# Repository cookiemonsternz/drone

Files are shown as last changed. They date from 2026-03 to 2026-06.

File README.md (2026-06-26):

# F<sub>~ish</sub>PV

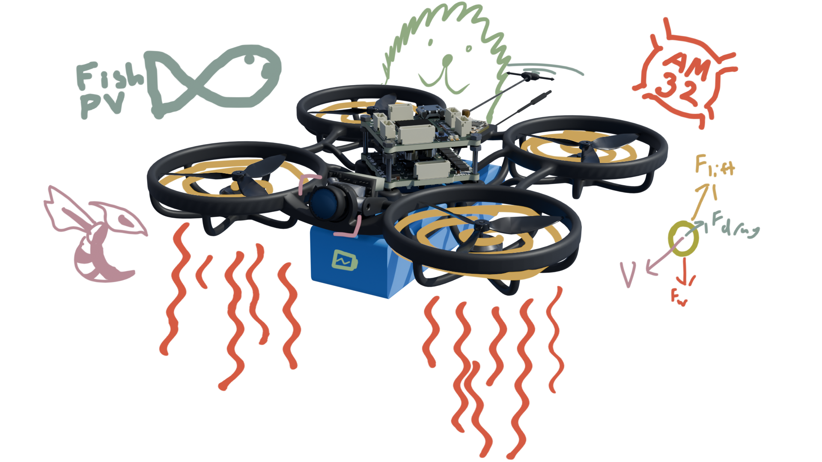
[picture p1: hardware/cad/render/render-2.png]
Render

_Tinywhoop drone with custom ESC, FC, and frame._

## What?

F<sub>\~ish</sub>PV is a open source, custom stack, 75mm tinywhoop drone design.
It utilises AM32 for the ESC firmware and Betaflight for the flight controller. 

Custom components include a from-scratch frame, designed for 3d printing (in HP-12-CF filament), a fully custom 15A ESC, and a custom FC. 

**The ESC:**
- 15A Continuous
- 20A Peak for 5s (unverified :O)
- 2S Battery (only)
- AM32 Firmware
- DSHOT Communication + Voltage telemetry
- Current Sense
  
**The FC:**
- STM32F405
- OSD: MAX7456
- IMU: ICM-42688-P
- 128Mbit blackbox
- USB DFU
- 2S Battery (only)
- BEC: 5V/0.5A Max
- Mounting: 25.5x25.5
- Dimensions: 28.3x28.3x10
- UART: 1, 4, 5
- Buzzer!

## Why?

To be honest a lot of this project was just for my own learning, but I also wanted to make a drone that could be generally cheaper than buying prebuilt components. I've somewhat achieved this, with a net cost of ~$300 USD, but obviously this cost is higher due to lack of bulk pricing. Unfortunately, some parts I wanted to design from scratch proved to be infeasible within the scope of this project (namely vtx and vrx) so that has driven the total cost up slightly.

Aside from that, drones are cool, and tinywhoops especially so. The main benefit in my opinion is the crashability. The size makes it much more feasible to use alternative manufacturing options. As I mentioned earlier, I designed this with HP-12-CF filament in mind, but HP-12 MJF Nylon is also a very feasible option that could potentially be quite durable (I have simulated both, but it is worth noting that the CF simulations will not be entirely accurate due to the weakness along layer lines not being modelled).

## How to use?

The drone assembly should be reasonably straightforward, I have provided a wonderful exploded diagram that should help significantly:

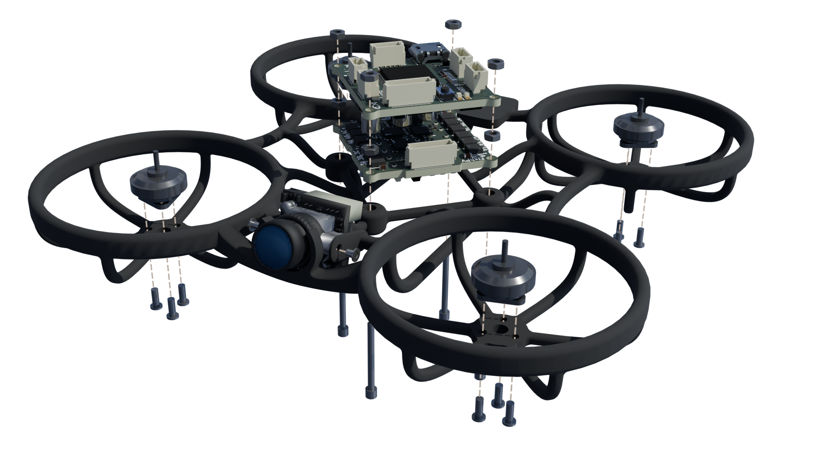
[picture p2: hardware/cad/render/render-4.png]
Exploded Diagram

Feel free to assemble it how you see fit, I'll likely change some things in the future but I'd like to try this configuration for now.

For wiring, theres this handy diagram. A lot of it just uses jst-sh connectors (as conformant to the [Betaflight Connector Standard](https://betaflight.com/docs/development/manufacturer/connector-standard)).

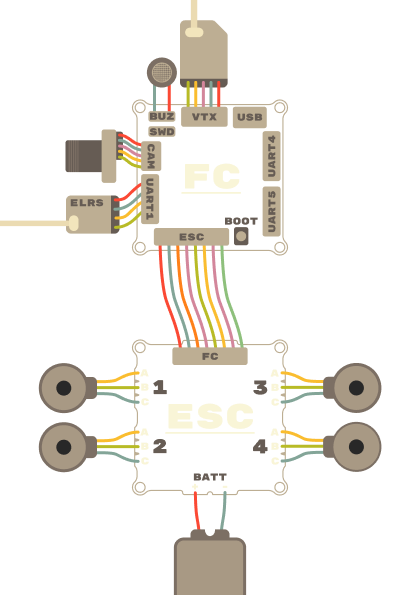
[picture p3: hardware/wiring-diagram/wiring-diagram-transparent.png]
Wiring Diagram


The ELRS receiver and vtx module can be attached however you see fit. I have included a mounting plate, and myself intend to use hot glue but velcro, etc. are also options.

Aside from the physical assembly, the FC and ESC must be flashed as outlined below or in the respective folders in **firmware/**. As I didn't want to do a bunch of pull requests for a likely one off design, I have provided compiled versions of the firmware. If you want to compile yourself, check out my forks of [Betaflight](https://github.com/cookiemonsternz/betaflight) and [AM32](https://github.com/cookiemonsternz/AM32). AM32 was built using github actions, and Betaflight was built locally using WSL as outlined in [the documentation](https://betaflight.com/docs/development#development).

### ESC Firmware

The esc runs on AM32, an open source ESC firmware which manages motor control, communication via dshot, and telemetry.

#### Bootloader

First of all, we need to install the bootloader onto each of the chips. For each chip, connect via the exposed swd/io interface, as outlined in the following table, and flash the bootloader hex file from **firmware/esc/bootloader/**

| MCU | SWDIO | SWDCLK |
|-----|---|---|
| 1 | TP1 | TP2 |
| 2 | TP3 | TP4 |
| 3 | TP6 | TP5 |
| 4 | TP8 | TP7 |

#### Firmware

Next connect the flight controller (which should be flashed before this step),
visit [am32 configurator](https://am32.ca/) and upload the firmware from **firmware/esc/**

---

### FC Firmware

Installation follows the same procedure as pretty much any flight controller.
Visit [Betaflight Configurator](https://app.betaflight.com/) and select firmware flasher. 

At the bottom of the screen, press load local:
Configurator
Upload the hex file and then hit flash!

That's it, should be all configured (maybe) but I'd reccomend going through and doing the regular adjustments and calibration.

## Renders

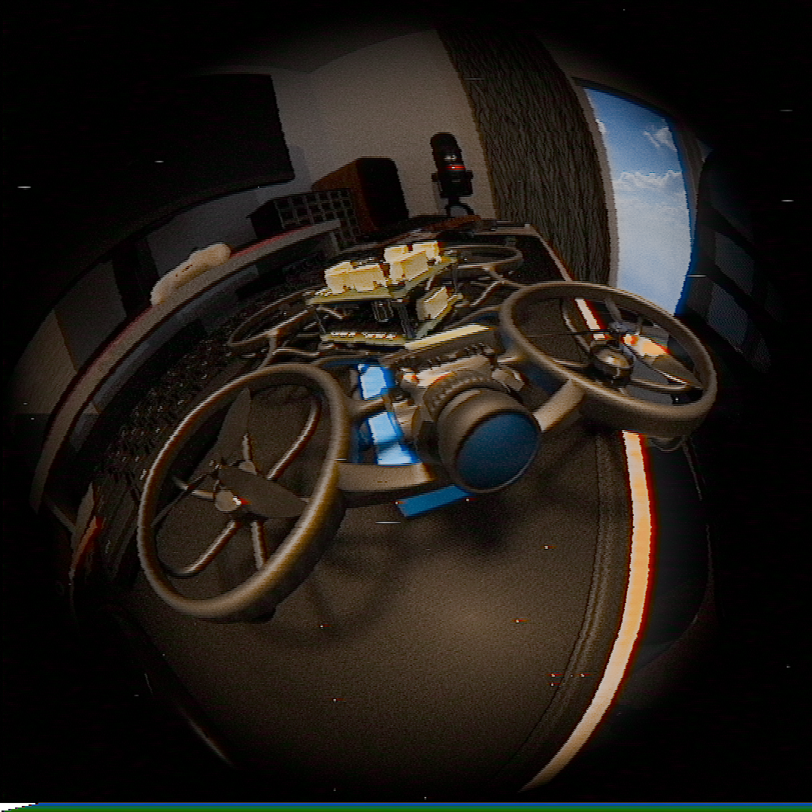
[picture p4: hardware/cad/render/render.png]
Render 1

Render 2
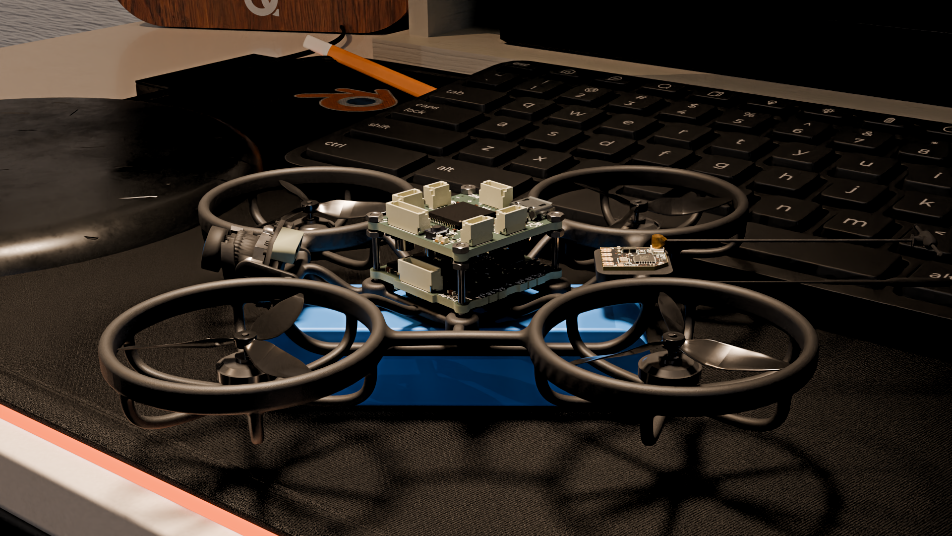
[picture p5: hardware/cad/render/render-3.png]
Render 3


## Zine Page

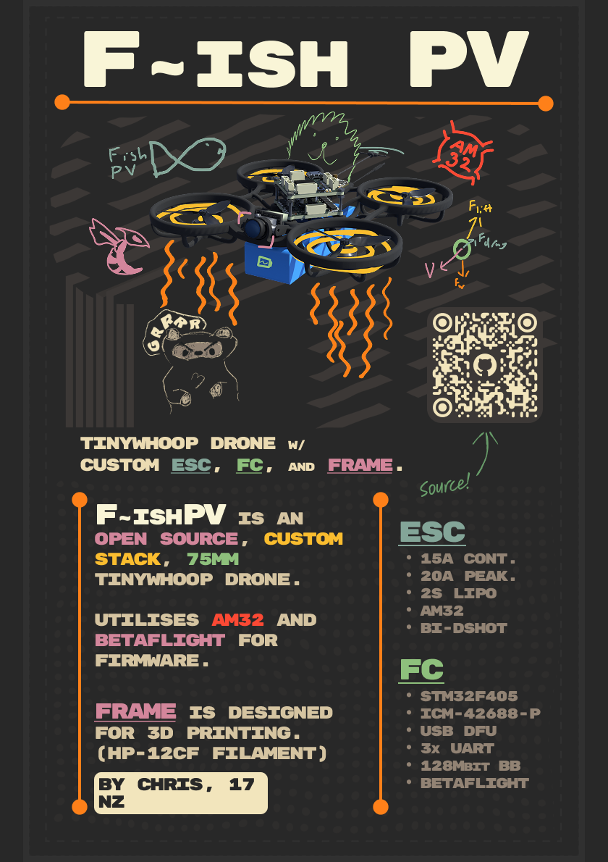
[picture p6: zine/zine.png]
Zine Page


## Simulations

I ran a handful of simulations in FreeCAD, and these are just a small sample of the results I got. 

First up, a collision where the battery is impacted. Think the drone just dropping onto the ground. This is for a collision at approximately 50km/h assuming a collision time of 25ms and a net mass of around 250g (so probably a bit extreme), to be specific, I modelled a force of 150N.
Battery collision
As you can see, there is even deflection across all four mounting posts for the FC/ESC stack, which will result in minimal tensile strain on the PCBs (which is the typical cause of damage).

Another type of collision I modelled is just a collision directly to the prop guards. Again, a 150N force which would be ~50km/h as mentioned above.
Prop guard collision
There is a lot of displacement on the prop guard but it is effectively dissipated and won't have much impact on the electronics, which is the main thing to be worried about. 
For this specific impact, I would be reasonably worried about damage to the frame, but for most crashes (which are probably not at 50km/h) it should be perfectly fine.

Many more simulations at different loads and also modelling the HP-12 MJF material can be found [here](https://github.com/cookiemonsternz/drone/blob/main/journals/journal-14-05-2026.md).

## BOM

| Desc | Value | Package | Link | Num | Needed | MOQ | MOQ Price | Net Price | Running Total |
|---|---|---|---|-----|---|-----|---|---|---|
| **Capacitors** | | | | | | | | | |
| 10nF Ceramic Cap, 0402 | 10nF | 0402 | https://www.lcsc.com/product-detail/C15195.html | 1 | 1 | 100 | $0.16 | $0.16 | $0.16 |
| 22nF Ceramic Cap, 0402 | 22nF | 0402 | https://www.lcsc.com/product-detail/C1532.html | 2 | 2 | 100 | $0.21 | $0.21 | $0.37 |
| 100nF Ceramic Cap, 0402 | 100nF | 0402 | https://www.lcsc.com/product-detail/C1525.html | 44  | 44 | 100 | $0.15 | $0.15 | $0.52 |
| 1uF Ceramic Cap, 0402 | 1uF | 0402 | https://www.lcsc.com/product-detail/C52923.html | 4 | 4 | 100 | $0.4 | $0.40 | $0.92 |
| 2.2uF Ceramic Cap, 0402 | 2.2uF | 0402 | https://www.lcsc.com/product-detail/C12530.html | 3 | 3 | 100 | $0.32 | $0.32 | $1.24 |
| 4.7uF Capacitors, 0603 | 4.7uF | 0603 | https://www.lcsc.com/product-detail/C19666.html | 4 | 4 | 10  | $0.11 | $0.11 | $1.35 |
| 22uF Capacitors, 0603 | 22uF | 0603 | https://www.lcsc.com/product-detail/C86295.html | 4 | 4 | 10  | $0.16 | $0.16 | $1.51 |
| 22uF Capacitors, 0805 | 22uF | 0805 | https://www.lcsc.com/product-detail/C29277.html | 2 | 2 | 10  | $0.21 | $0.21 | $1.72 |
| 22uF Electrolytic Cap, SMD | 22uF | SMD,D4xL5.4mm  | https://www.lcsc.com/product-detail/C335975.html | 2 | 2 | 20  | $0.48 | $0.48 | $2.20 |
| 47uF Electrolytic Cap, SMD | 47uF | SMD,D4xL5.4mm  | https://www.lcsc.com/product-detail/C87853.html | 2 | 2 | 20  | $0.53 | $0.53 | $2.73 |
| **Resistors** | | | | | | | | | |
| 22R Resistors, 0402 | 22r | 0402 | https://www.lcsc.com/product-detail/C2906914.html | 26  | 26 | 100 | $0.07 | $0.07 | $2.80 |
| 75R Resistor, 0402 | 75? | 0402 | https://www.lcsc.com/product-detail/C25133.html | 4 | 4 | 100 | $0.09 | $0.09 | $2.89 |
| 1k Resistor, 0402 | 1k? | 0402 | https://www.lcsc.com/product-detail/C11702.html | 17  | 17 | 100 | $0.11 | $0.11 | $3.00 |
| 2.2k Resistor, 0402 | 2.2k? | 0402 | https://www.lcsc.com/product-detail/C25879.html | 3 | 3 | 100 | $0.10 | $0.10 | $3.10 |
| 10k Resistor, 0402 | 10k? | 0402 | https://www.lcsc.com/product-detail/C25744.html | 6 | 6 | 100 | $0.13 | $0.13 | $3.23 |
| 100k Resistor, 0402 | 100k? | 0402 | https://www.lcsc.com/product-detail/C25741.html | 4 | 4 | 100 | $0.09 | $0.09 | $3.32 |
| 10k Resistor Arrays, 0603x4 | 10k | 0603x4 | https://www.lcsc.com/product-detail/C110924.html | 6 | 6 | 50  | $0.55 | $0.55 | $3.87 |
| 124k Voltage Div Resistor, 0603 | 124k | 0603 | https://www.lcsc.com/product-detail/C2933136.html | 1 | 1 | 100 | $0.11 | $0.11 | $3.98 |
| 0.5m Shunt Resistor, 1216 | 0.5mr | 1216 | https://www.lcsc.com/product-detail/C2688874.html | 1 | 1 | 1 | $1.01 | $1.01 | $4.99 |
| **Diodes** | | | | | | | | | |
| Red LED | | 0603 | https://www.lcsc.com/product-detail/C51933292.html | 1 | 1 | 50  | $0.13 | $0.13 | $5.12 |
| Blue LED | | 0603 | https://www.lcsc.com/product-detail/C2288.html | 1 | 1 | 50  | $0.51 | $0.51 | $5.63 |
| Green LED | | 0603 | https://www.lcsc.com/product-detail/C22371297.html | 1 | 1 | 50  | $0.71 | $0.71 | $6.34 |
| Schottky Diode | | SOD-323 | https://www.lcsc.com/product-detail/C191023.html | 2 | 2 | 50  | $0.54 | $0.54 | $6.88 |
| **Connectors** | | | | | | | | | |
| Camera Conn | 3P SH | SMD,P=1mm | https://www.lcsc.com/product-detail/C7430452.html | 1 | 1 | 5 | $0.34 | $0.34 | $7.22 |
| UART Conns | 4P SH | SMD,P=1mm | https://www.lcsc.com/product-detail/C7433440.html | 3 | 3 | 10  | $0.35 | $0.35 | $7.57 |
| VTX Conn | 5P SH | SMD,P=1mm | https://www.lcsc.com/product-detail/C2845373.html | 1 | 1 | 5 | $0.58 | $0.58 | $8.15 |
| ESC Conns | 8P SH | SMD,P=1mm | https://www.lcsc.com/product-detail/C2764202.html | 2 | 2 | 5 | $0.61 | $0.61 | $8.76 |
| USB Micro B Conn | | SMD | https://www.lcsc.com/product-detail/C404969.html | 1 | 1 | 10  | $0.41 | $0.41 | $9.17 |
| **FC** | | | | | | | | | |
| STM32F405 (U1) | | LQFP-64(10x10) | https://www.lcsc.com/product-detail/C15742.html | 1 | 1 | 1 | $3.93 | $3.93 | $13.10 |
| ICM-42668-P : IMU (U2) | | LGA-14(2.5x3)  | https://www.lcsc.com/product-detail/C1850418.html | 1 | 1 | 1 | $12.88 | $12.88 | $25.98 |
| MAX-7456eui+ (U3) | Source: Aliexpress | | https://www.aliexpress.com/item/33005990891.html | 1 | 1 | 1 | $4.28 | $4.28 | $30.26 |
| BL8072CLTR-3.3 (3.3V LDO) (U6) | 3.3V | SOT-223-3 | https://www.lcsc.com/product-detail/C843780.html | 1 | 1 | 5 | $0.99 | $0.99 | $31.25 |
| SGM2212-3.3XKC3G/TR (IMU LDO) (U7) | 3.3V | SOT-223-3 | https://www.lcsc.com/product-detail/C3294699.html | 1 | 1 | 1 | $0.61 | $0.61 | $31.86 |
| W25Q128JVSIQ TR (Flash) (U8) | | SOIC-8-208mil  | https://www.lcsc.com/product-detail/C97521.html | 1 | 1 | 1 | $2.32 | $2.32 | $34.18 |
| TPS62173DSG (5V BEC) (U4, U5) | 5V | WSON-8-EP(2x2) | https://www.lcsc.com/product-detail/C181384.html | 2 | 2 | 1 | $0.93 | $1.86 | $36.04 |
| BMP280 Baro (U10) | | LGA-8(2x2.5) | https://www.lcsc.com/product-detail/C83291.html | 1 | 1 | 1 | $6.90 | $6.90 | $42.94 |
| 27MHz Crystal (Y1) | 27MHz | SMD3225-4P | https://www.lcsc.com/product-detail/C9008.html | 1 | 1 | 10  | $0.77 | $0.77 | $43.71 |
| 8MHz Crystal w/ Caps (Y2) | 8MHz | SMD3213-3P | https://www.lcsc.com/product-detail/C907975.html | 1 | 1 | 5 | $1.05 | $1.05 | $44.76 |
| BEC Inductors (L1, L2) | 2.2uH | 0806 | https://www.lcsc.com/product-detail/C695610.html | 1 | 1 | 5 | $0.82 | $0.82 | $45.58 |
| BOOT Button (SW2) | | SMD,4x3mm | https://www.lcsc.com/product-detail/C720477.html | 1 | 1 | 10  | $0.54 | $0.54 | $46.12 |
| Reverse Pol. Mosfet (Q1) | | SOT-23 | https://www.lcsc.com/product-detail/C15127.html | 1 | 1 | 10  | $0.59 | $0.59 | $46.71 |
| **ESC** | | | | | | | | | |
| 470nH Inductor, 0603 | 470nH | 0603 | https://www.lcsc.com/product-detail/C113132.html | 1 | 1 | 10  | $0.47 | $0.47 | $47.18 |
| Mosfets (SP40N03GNJ) | | PDFN-8L(3x3) | https://www.lcsc.com/product-detail/C22466709.html | 24  | 24 | 5 | $1.05 | $5.25 | $52.43 |
| ESC MCUs (AT32F421G8U7) | | QFN-28-EP(4x4) | https://www.lcsc.com/product-detail/C2765098.html | 4 | 4 | 1 | $0.85 | $3.40 | $55.83 |
| ESC Mosfet Gate Drivers (NSG2065Q) | | QFN-24-EP(4x4) | https://www.lcsc.com/product-detail/C41414478.html | 4 | 4 | 1 | $0.48 | $1.92 | $57.75 |
| Current Sense Amplifier (INA180B2) | | SOT-23-5 | https://www.lcsc.com/product-detail/C2057844.html | 1 | 1 | 1 | $0.26 | $0.26 | $58.01 |
| 8V Regulator (LMR51420YDDCR) | | SOT-23-6 | https://www.lcsc.com/product-detail/C5383002.html | 1 | 1 | 1 | $0.83 | $0.83 | $58.84 |
| 3.3V Regulator (TLV76733DRVR) | | WSON-6(2x2) | https://www.lcsc.com/product-detail/C2848334.html | 1 | 1 | 5 | $1.01 | $1.01 | $59.85 |
| **BOARDS** | | | | | | | | | $59.85 |
| ESC Board + Stencil (JLCPCB) | | | | | | | | $5.29 | $65.14 |
| FC Board + Stencil (JLCPCB) | | | | | | | | $5.21 | $70.35 |
| Frame (JLC3DP, HP-12-CF) | | | | | | | | $5.56 | $75.91 |
| **MODULES** | | | | | | | | | $75.91 |
| ELRS Receiver (RP1 Nano Clone) | | | https://www.aliexpress.com/item/1005005236594556.html | 1 | 1 | 1 | $12.62 | $12.62 | $88.53 |
| CaddX Ant Camera | | | https://www.aliexpress.com/item/1005008798090166.html | 1 | 0 | 1 | $12.99 | $0.00 | $88.53 |
| PandaRC Nano25 VTX | | | https://www.aliexpress.com/item/1005011701933149.html | 1 | 0 | 1 | $18.94 | $0.00 | $88.53 |
| Happymodel RS1102 13500KV Motors | | | https://kiwiquads.co.nz/product/happymodel-rs1102-kv13500-brushless-motor-for-m8-freestyle/ | 4 | 4 | 4 | $11.11 | $44.44 | $132.97 |
| 40mm 1.5mm Shaft Triblade Props | | | https://www.aliexpress.com/item/1005010520091463.html | 4 | 4 | 16  | $6.37 | $6.37 | $139.34 |
| 2s 680mah lipo | | | https://kiwiquads.co.nz/product/betafpv-lava-series-ii-2s-680mah-95c/ | 1 | 1 | 1 | $14.62 | $14.62 | $153.96 |
| Radiomaster T8L | | | https://radiomasterrc.com/products/t8l-radio-controller?variant=47089026465984 | 1 | 1 | 1 | $34.99 | $34.99 | $188.95 |
| TS832 Receiver | | | https://www.aliexpress.com/item/1005012037139433.html | 1 | 0 | 1 | $43.86 | $0.00 | $188.95 |

| Totals (EXCL. VIDEO SYSTEM) | | |
|---|---|---|
| Vendor | Net | W/ Shipping |
| JLCPCB / 3DP | $16.06  | $41.99 |
| LCSC | $55.16  | $55.55 |
| Aliexpress | $23.27  | $22.95 |
| Kiwiquads | $59.05  | $61.96 |
| Radiomaster | $34.99  | $44.99 |
| JLCPCB | $10.50  | $32.06 |
| --- | $199.03 | $259.50 |

## Cad Links

All of the CAD source files can be found on [Onshape](https://cad.onshape.com/documents/5b69b7ad5dc2bcb1a562cae6/w/28cfd389aaff8b3000581458/e/21531bda6c88e5e5db7731e6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). 
The physics simulations can be found in the FreeCAD project under **hardware/cad/sim/**

## Directory Structure

- **firmware/**
  - **esc/** - ESC Firmware (AM32)
  - **fc/** - FC Firmware (Betaflight)
- **hardware/**
    - **bom/** - BOM Files (CSV and LibreOffice Calc)
    - **cad/** - CAD Files
      - **render/** - Files for rendering (inc. gltf models) *Note that the Blender file for the renders exceeds the maximum file size for Github, it can be found in [Google Drive](https://drive.google.com/file/d/1S7Jwgq-ZpHFBb5yz26d0MQlCH4Twi4XQ/view?usp=sharing).*
      - **sim/** - FreeCAD files for FEM Analysis
    - **esc/** - ESC KiCad Project
      - **production/** - Production files (Gerber, etc.)
    - **fc/** - FC KiCad Project
      - **production/** - Production files (Gerber, etc.)
    - **lib/** - Shared KiCad libraries
    - **wiring-diagram/** - Wiring diagram
- **journals/**
- **zine/** - Zine page :)

## References
[Betaflight Documentation](https://betaflight.com/docs/development)

[AM32 Documentation](https://wiki.am32.ca/general/docs.html) - Especially re [Hardware Design](https://wiki.am32.ca/development/Hardware-Design.html)

[AcciFPV FC](https://www.pcbway.com/project/shareproject/Acci_FPV_Flight_Controller_Betaflight_STM32F405_AT32F435_48fb0ecb.html)

[Hack Club Blueprint - FC Guided Project](https://blueprint.hackclub.com/starter-projects/flightcontroller)

[JustFPV ESC Design](https://www.youtube.com/watch?v=TwAmmPxOpTM)

AM32 & Betaflight Discords

And various others which I have forgotten.

#### This project was created for [Hack Club](https://hackclub.com/) - [Fallout](https://fallout.hackclub.com/)

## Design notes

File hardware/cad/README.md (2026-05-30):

# CAD

## Mesh

- **drone.blend** - *Full blender assembly, merged and fixed parts exported from here. Not that exports from Blender do not successfully upload to jlc3dp, to fix this import and then export in Cura.*
- **frame-merged.stl** - *Merged frame model, production file incl. camera mount and batt. support.*
- **frame.stl** - *Main frame model, excl. camera mount and batt. support, do not produce.*
- **camera-mount.stl** - *Camera mount model, do not produce*
- **battery-support.stl** - *Battery support model, do not produce*

## Parametric

All CAD design source can be found [on Onshape](https://cad.onshape.com/documents/5b69b7ad5dc2bcb1a562cae6/w/28cfd389aaff8b3000581458/e/21531bda6c88e5e5db7731e6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).

- **frame.step** - *Main frame model, excl. camera mount and batt. support, do not produce*
- **camera-mount.step** - *Camera mount model, do not produce*
- **battery-support.step** - *Battery support model, do not produce*

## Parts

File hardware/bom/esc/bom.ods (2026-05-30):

Basic? | Desc | Value | Part Details | Package | Link | Num | Needed | MOQ | MOQ Price | Net Price | Running Total
TRUE | Mosfet Gate Resistors (R1-R6, ...) | 22r | -55℃~+155℃ 22Ω 50V 62.5mW Thick Film Resistor ±1% ±100ppm/℃ 0402 Chip Resistor - Surface Mount ROHS | 0402 | https://www.lcsc.com/product-detail/C2906914.html | 24 | 24 | 100 | $0.07 | $0.07 | $0.07
FALSE | BEMF Div Resistor (R9, R12, R15, ...) | 10k | -55℃~+155℃ 10kΩ 50V 62.5mW Thick Film Resistor ±100ppm/℃ ±5% 0402 Chip Resistor - Surface Mount ROHS | 0402 | https://www.lcsc.com/product-detail/C2906861.html | 12 | 12 | 100 | $0.06 | $0.06 | $0.05
TRUE | BEMF Div Resistor (R11, R13, R16, ...) | 1k | -55℃~+155℃ 1kΩ 50V 62.5mW Thick Film Resistor ±1% ±100ppm/℃ 0402 Chip Resistor - Surface Mount ROHS | 0402 | https://www.lcsc.com/product-detail/C2906864.html | 12 | 12 | 100 | $0.07 | $0.07 | $0.06
FALSE | BEMF Div Resistor (R10, R14, R17, ...) | 10k | -55℃~+155℃ 10kΩ 50V 62.5mW Thick Film Resistor ±100ppm/℃ ±5% 0402 Chip Resistor - Surface Mount ROHS | 0402 | https://www.lcsc.com/product-detail/C2906861.html | 12 | 12 | 100 | $0.06 | $0.06 | $0.08
TRUE | Bootstrap Cap (C1-C3, ...) | 100nF | 100nF 50V X7R ±10% 0402 Multilayer Ceramic Capacitors MLCC - SMD/SMT ROHS | 0402 | https://jlcpcb.com/partdetail/291005-CL05B104KB54PNC/C307331 | 12 | 12 |  | $0.0043 | #DIV/0! | $0.13
TRUE | VDD Bypass Caps (C8-C10, ...) | 10uF | 10uF 25V X5R ±20% 0603 Multilayer Ceramic Capacitors MLCC - SMD/SMT ROHS | 0603 | https://jlcpcb.com/partdetail/97651-CL10A106MA8NRNC/C96446 | 12 | 12 |  | $0.0180 | #DIV/0! | $0.35
FALSE | Volt Sense Div Resistor (R18, ...) | 10k | -55℃~+155℃ 10kΩ 50V 62.5mW Thick Film Resistor ±100ppm/℃ ±5% 0402 Chip Resistor - Surface Mount ROHS | 0402 | https://www.lcsc.com/product-detail/C2906861.html | 4 | 4 | 100 | $0.06 | $0.06 | $0.35
TRUE | Volt Sense Div Resistor (R19, ...) | 100k | -55℃~+155℃ 100kΩ 50V 62.5mW Thick Film Resistor ±1% ±100ppm/℃ 0402 Chip Resistor - Surface Mount ROHS | 0402 | https://www.lcsc.com/product-detail/C2906859.html | 4 | 4 | 100 | $0.06 | $0.06 | $0.35
TRUE | ESC Indicator LED (D1, ...) | NA | -40℃~+85℃ 1.8V~2.4V 120° 20mA 300mcd 40mW 615nm~630nm 645nm Discrete Diode Red Water Clear 0603 LED Indication - Discrete ROHS | 0603 | https://jlcpcb.com/partdetail/Hubei_KENTOElec-KT0603R/C2286 | 4 | 4 |  | $0.0065 | #DIV/0! | $0.38
TRUE | ESC Indicator LED Resistor (R20, ...) | 2.2k | -55℃~+155℃ 2.2kΩ 50V 62.5mW Thick Film Resistor ±1% ±100ppm/℃ 0402 Chip Resistor - Surface Mount ROHS | 0402 | https://www.lcsc.com/product-detail/C2906920.html | 4 | 4 | 100 | $0.06 | $0.06 | $0.38
TRUE | ESC Decoupling Capacitors (C4, C6, ...) | 100nF | 100nF 50V X7R ±10% 0402 Multilayer Ceramic Capacitors MLCC - SMD/SMT ROHS | 0402 | https://jlcpcb.com/partdetail/291005-CL05B104KB54PNC/C307331 | 8 | 8 |  | $0.0043 | #DIV/0! | $0.42
FALSE | Mosfets (Q1-Q6, ...) | NA | -55℃~+150℃ 1 N-channel 1.5V 1.675nF 2.9mΩ@10V、4.2mΩ@4.5V 26nC@20V 31pF 395pF 40V 55W 75A N-Channel PDFN-8L(3x3) MOSFETs ROHS | PDFN-8L(3x3) | https://jlcpcb.com/partdetail/Siliup-SP40N03GNJ/C22466709 | 24 | 24 |  | $0.2194 | #DIV/0! | $5.68
TRUE | Dshot Resistor (R8, ...) | 1k | -55℃~+155℃ 1kΩ 50V 62.5mW Thick Film Resistor ±1% ±100ppm/℃ 0402 Chip Resistor - Surface Mount ROHS | 0402 | https://www.lcsc.com/product-detail/C2906864.html | 4 | 4 | 100 | $0.07 | $0.07 | $5.69
FALSE | Boot0 Resistor (R7, ...) | 10k | -55℃~+155℃ 10kΩ 50V 62.5mW Thick Film Resistor ±100ppm/℃ ±5% 0402 Chip Resistor - Surface Mount ROHS | 0402 | https://www.lcsc.com/product-detail/C2906861.html | 4 | 4 | 100 | $0.0005 | $0.00 | $5.69
TRUE | NRST Capacitor (C5, ...) | 100nF | 100nF 16V X7R ±10% 0402 Multilayer Ceramic Capacitors MLCC - SMD/SMT ROHS | 0402 | https://jlcpcb.com/partdetail/1877-CL05B104KO5NNNC/C1525 | 4 | 4 |  | $0.0013 | #DIV/0! | $5.70
TRUE | Ferrite Bead (FB1, ...) | 100R-100MHz | 1 100Ω@100MHz 150mΩ 800mA ±25% 0805 Ferrite Beads ROHS | 0805 | https://jlcpcb.com/partdetail/Sunlord-GZ2012D101TF/C1015 | 4 | 4 |  | $0.0149 | #DIV/0! | $5.76
FALSE | ESC MCU (U2, ...) | NA | -40℃~+105℃ 120MHz 16KB 2.4V~3.6V 23 32 Bit 64KB ARM Cortex-M4 Built-in+External FLASH QFN-28-EP(4x4) Microcontrollers (MCU/MPU/SOC) ROHS | QFN-28-EP(4x4) | https://jlcpcb.com/partdetail/ARTERY-AT32F421G8U7/C2765098 | 4 | 4 |  | $0.8444 | #DIV/0! | $9.13
FALSE | ESC Mosfet Gate Driver (U1, ...) | NA | -40℃~+125℃ 1.2A 1.5A 15ns 40ns 5V~20V 700uA IGBT、MOSFET Three Phase Under Voltage Protection QFN-24-EP(4x4) Gate Drivers ROHS | QFN-24-EP(4x4) | https://jlcpcb.com/partdetail/WXNSIC-NSG2065Q/C41414478 | 4 | 4 |  | $0.4667 | #DIV/0! | $11.00
 | MAIN BOARD COMPONENTS |  |  |  |  |  |  |  |  | #DIV/0! | $11.00
 | Current Sense Amplifier (U3) | NA | -26V~+26V -40℃~+125℃ 0.05uA 1 100dB 100nA 197uA 1uV/℃ 2.7V~5.5V 200mV~26V 210kHz 25uV 2V/us 40nV/√Hz@1kHz 5.5V 50V/V 8mA SOT-23-5 Current Sense Amplifiers ROHS | SOT-23-5 | https://jlcpcb.com/partdetail/TexasInstruments-INA180B2IDBVR/C2861539 | 1 | 1 |  | $0.4206 | #DIV/0! | $11.42
FALSE | 8V Regulator (U11) | NA | -40℃~+150℃@(TJ) 1 1.1MHz 2A 4.5V~36V 40uA 600mV~34.2V Adjustable Buck Buck Built-in Yes SOT-23-6 DC-DC Converters ROHS | SOT-23-6 | https://jlcpcb.com/partdetail/TexasInstruments-LMR51420YFDDCR/C7296200 | 1 | 1 |  | $1.1808 | #DIV/0! | $12.60
FALSE | 3.3V Regulator (U10) | NA | -40℃~+125℃@(Tj) 1 1.4V@(1A) 16V 1A 3.3V 46dB@(1MHz) 50uA 60uVrms Fixed Over Current Protection、Over Temperature Protection、Soft Start Positive WSON-6(2x2) Voltage Regulators - Linear, Low Drop Out (LDO) Regulators ROHS | WSON-6(2x2) | https://jlcpcb.com/partdetail/TexasInstruments-TLV76733DRVR/C2848334 | 1 | 1 |  | $0.2151 | #DIV/0! | $12.82
FALSE | Shunt Resistor (R21) | 0.5mr | 0.5mΩ 5W Current Sense Resistor SMD ±1% ±50ppm/℃ 1216 Current Sense Resistors / Shunt Resistors ROHS | 1216 | https://jlcpcb.com/partdetail/Isabellenhuette-BVN_Z_R0005_10/C2688874 | 1 | 1 |  | $0.5238 | #DIV/0! | $13.12
FALSE | Inductor (L1) | 470nH | 3.8A 38mΩ 470nH 4A ±20% 0603 Power Inductors ROHS | 0603 | https://jlcpcb.com/partdetail/XR-XRIM160808SR47MBCD/C48391583 | 1 | 1 |  | $0.1348 | #DIV/0! | $13.26
TRUE | Main Board Decoupling Capacitors (C57, C58, C61, C62) | 100nF | 100nF 50V X7R ±10% 0402 Multilayer Ceramic Capacitors MLCC - SMD/SMT ROHS | 0402 | https://jlcpcb.com/partdetail/291005-CL05B104KB54PNC/C307331 | 4 | 4 |  | $0.0043 | #DIV/0! | $13.27
TRUE | Main Board Filtering Capacitors (C59, C60, C63, C64) | 22uF | 22uF 25V X5R ±20% 0805 Multilayer Ceramic Capacitors MLCC - SMD/SMT ROHS | 0805 | https://jlcpcb.com/partdetail/46786-CL21A226MAQNNNE/C45783 | 4 | 4 |  | $0.0316 | #DIV/0! | $13.40
FALSE | Main Board Voltage Div Resistor (R83) | 10k | -55℃~+155℃ 10kΩ 50V 62.5mW Thick Film Resistor ±100ppm/℃ ±5% 0402 Chip Resistor - Surface Mount ROHS | 0402 | https://jlcpcb.com/partdetail/FOJAN-FRC0402J103TS/C2906885 | 1 | 1 |  | $0.0005 | #DIV/0! | $13.40
FALSE | Main Board Voltage Div Resistor (R82) | 124k | -55℃~+155℃ 100mW 124kΩ 75V Thick Film Resistor ±1% ±100ppm/℃ 0603 Chip Resistor - Surface Mount ROHS | 0603 | https://jlcpcb.com/partdetail/23515-0603WAF1243T5E/C22788 | 1 | 1 |  | $0.0014 | #DIV/0! | $13.40
FALSE | JST Connector (J1) | NA | -25℃~+85℃ 1 10mm 1A 1mm 1x8P 2.9mm 4.32mm 50V 8 8P Auxiliary Solder Pin Copper alloy PA SH Surface Mount, Right Angle Tin UL94V-0 White SMD,P=1mm,卧贴 Wire To Board Connector ROHS | SMD,P=1mm,Surface Mount，Right Angle | https://jlcpcb.com/partdetail/JST-SM08B_SRSS_TB_LF_SN/C160407 | 1 | 1 |  | $0.3062 | #DIV/0! | $13.71

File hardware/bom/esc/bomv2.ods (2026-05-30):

Desc | Value | Package | Link | Num | Needed | MOQ | MOQ Price | Net Price | Running Total
22R Resistors, 0402 | 22r | 0402 | https://www.lcsc.com/product-detail/C2906914.html | 24 | 24 | 100 | $0.07 | $0.07 | $0.07
1k Resistors, 0402 | 1k | 0402 | https://www.lcsc.com/product-detail/C2906899.html | 16 | 16 | 100 | $0.06 | $0.06 | $0.13
10k Resistors, 0402 | 10k | 0402 | https://www.lcsc.com/product-detail/C2906861.html | 4 | 4 | 100 | $0.06 | $0.06 | $0.19
10k Resistor Arrays, 0603x4 | 10k | 0603x4 | https://www.lcsc.com/product-detail/C110924.html | 6 | 6 | 50 | $0.55 | $0.55 | $0.74
100k Resistor, 0402 | 100k | 0402 | https://www.lcsc.com/product-detail/C2906859.html | 1 | 1 | 100 | $0.06 | $0.06 | $0.80
2.2k LED Resistors, 0402 | 2.2k | 0402 | https://www.lcsc.com/product-detail/C2906920.html | 1 | 1 | 100 | $0.06 | $0.06 | $0.86
124k Voltage Div Resistor, 0603 | 124k | 0603 | https://www.lcsc.com/product-detail/C2933136.html | 1 | 1 | 100 | $0.11 | $0.11 | $0.97
0.5m Shunt Resistor, 1216 | 0.5mr | 1216 | https://www.lcsc.com/product-detail/C2688874.html | 1 | 1 | 1 | $1.01 | $1.01 | $1.98
100nF Capacitors, 0402 | 100nF | 0402 | https://www.lcsc.com/product-detail/C5137468.html | 28 | 28 | 100 | $0.10 | $0.10 | $2.08
4.7uF Capacitors, 0603 | 4.7uF | 0603 | https://www.lcsc.com/product-detail/C19666.html | 4 | 4 | 10 | $0.11 | $0.11 | $2.19
22uF Capacitors, 0603 | 22uF | 0603 | https://www.lcsc.com/product-detail/C86295.html | 4 | 4 | 10 | $0.16 | $0.16 | $2.35
22uF Capacitors, 0805 | 22uF | 0805 | https://www.lcsc.com/product-detail/C29277.html | 2 | 2 | 10 | $0.21 | $0.21 | $2.56
470nH Inductor, 0603 | 470nH | 0603 | https://www.lcsc.com/product-detail/C113132.html | 1 | 1 | 10 | $0.47 | $0.47 | $3.03
ESC Indicator LED | NA | 0603 | https://www.lcsc.com/product-detail/C51933292.html | 1 | 1 | 50 | $0.13 | $0.13 | $3.16
Mosfets (SP40N03GNJ) | NA | PDFN-8L(3x3) | https://www.lcsc.com/product-detail/C22466709.html | 24 | 24 | 5 | $1.05 | $5.25 | $8.41
ESC MCUs (AT32F421G8U7) | NA | QFN-28-EP(4x4) | https://www.lcsc.com/product-detail/C2765098.html | 4 | 4 | 1 | $0.85 | $3.40 | $11.81
ESC Mosfet Gate Drivers (NSG2065Q) | NA | QFN-24-EP(4x4) | https://www.lcsc.com/product-detail/C41414478.html | 4 | 4 | 1 | $0.48 | $1.92 | $13.73
Current Sense Amplifier (INA180B2) | NA | SOT-23-5 | https://www.lcsc.com/product-detail/C2057844.html | 1 | 1 | 1 | $0.26 | $0.26 | $13.99
8V Regulator (LMR51420YDDCR) | NA | SOT-23-6 | https://www.lcsc.com/product-detail/C5383002.html | 1 | 1 | 1 | $0.83 | $0.83 | $13.92
3.3V Regulator (TLV76733DRVR) | NA | WSON-6(2x2) | https://www.lcsc.com/product-detail/C2848334.html | 1 | 1 | 5 | $1.01 | $1.01 | $13.86
JST Connector (J1) | NA | SMD,P=1mm,Surface Mount，Right Angle | https://www.lcsc.com/product-detail/C160407.html | 1 | 1 | 5 | $1.58 | $1.58 | $13.80
Board + Stencil |  |  |  |  |  |  |  |  | $17.41
Board + Stencil (JLCPCB) | NA | NA | NA | NA | NA | NA | NA | $5.29 | $22.70
Totals |  |  |  |  |  |  |  |  | $22.70
Vendor | Total | With Shipping
LCSC | $17.42 | $25.25
JLCPCB | $5.29 | $14.77
Net
 | $22.71 | $40.02

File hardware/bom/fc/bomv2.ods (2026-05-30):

Desc | Value | Package | Link | Num | Needed | MOQ | MOQ Price | Net Price | Running Total
CAPS
10nF Ceramic Cap, 0402 | 10nF | 0402 | https://www.lcsc.com/product-detail/C15195.html | 1 | 1 | 100 | $0.16 | $0.16 | $1.24
22nF Ceramic Cap, 0402 | 22nF | 0402 | https://www.lcsc.com/product-detail/C1532.html | 2 | 2 | 100 | $0.21 | $0.21 | $2.25
100nF Ceramic Cap, 0402 | 100nF | 0402 | https://www.lcsc.com/product-detail/C1525.html | 16 | 16 | 100 | $0.15 | $0.15 | $0.15
1uF Ceramic Cap, 0402 | 1uF | 0402 | https://www.lcsc.com/product-detail/C52923.html | 4 | 4 | 100 | $0.4 | $0.40 | $1.72
2.2uF Ceramic Cap, 0402 | 2.2uF | 0402 | https://www.lcsc.com/product-detail/C12530.html | 3 | 3 | 100 | $0.32 | $0.32 | $0.92
22uF Electrolytic Cap, SMD | 22uF | SMD,D4xL5.4mm | https://www.lcsc.com/product-detail/C335975.html | 2 | 2 | 20 | $0.48 | $0.48 | $2.25
47uF Electrolytic Cap, SMD | 47uF | SMD,D4xL5.4mm | https://www.lcsc.com/product-detail/C87853.html | 2 | 2 | 20 | $0.53 | $0.53 | $0.87
DIODES
Blue LED (D1) |  | 0603 | https://www.lcsc.com/product-detail/C2288.html | 1 | 1 | 50 | $0.51 | $0.51 | $2.76
Green LED (D2) |  | 0603 | https://www.lcsc.com/product-detail/C22371297.html | 1 | 1 | 50 | $0.71 | $0.71 | $3.47
Schottky Diode (D3, D4) |  | SOD-323 | https://www.lcsc.com/product-detail/C191023.html | 2 | 2 | 50 | $0.54 | $0.54 | $4.01
RESISTORS
22R Resistor, 0402 | 22Ω | 0402 | https://www.lcsc.com/product-detail/C25092.html | 2 | 2 | 100 | $0.09 | $0.09 | $4.40
75R Resistor, 0402 | 75Ω | 0402 | https://www.lcsc.com/product-detail/C25133.html | 4 | 4 | 100 | $0.09 | $0.09 | $4.10
1k Resistor, 0402 | 1kΩ | 0402 | https://www.lcsc.com/product-detail/C11702.html | 1 | 1 | 100 | $0.11 | $0.11 | $4.53
2.2k Resistor, 0402 | 2.2kΩ | 0402 | https://www.lcsc.com/product-detail/C25879.html | 2 | 2 | 100 | $0.10 | $0.10 | $4.62
10k Resistor, 0402 | 10kΩ | 0402 | https://www.lcsc.com/product-detail/C25744.html | 2 | 2 | 100 | $0.13 | $0.13 | $4.19
100k Resistor, 0402 | 100kΩ | 0402 | https://www.lcsc.com/product-detail/C25741.html | 3 | 3 | 100 | $0.09 | $0.09 | $4.30
CONNECTORS
Camera Conn (J1) | 3P SH | SMD,P=1mm | https://www.lcsc.com/product-detail/C7430452.html | 1 | 1 | 5 | $0.34 | $0.34 | $4.96
UART Conns (J2, J8, J9) | 4P SH | SMD,P=1mm | https://www.lcsc.com/product-detail/C7433440.html | 3 | 3 | 10 | $0.35 | $0.35 | $5.31
VTX Conn (J4) | 5P SH | SMD,P=1mm | https://www.lcsc.com/product-detail/C2845373.html | 1 | 1 | 5 | $0.58 | $0.58 | $5.89
ESC Conn (J5) | 8P SH | SMD,P=1mm | https://www.lcsc.com/product-detail/C2764202.html | 1 | 1 | 5 | $0.61 | $0.61 | $6.50
OTHER
STM32F405 (U1) |  | LQFP-64(10x10) | https://www.lcsc.com/product-detail/C15742.html | 1 | 1 | 1 | $3.93 | $3.93 | $10.43
ICM-42668-P : IMU (U2) |  | LGA-14(2.5x3) | https://www.lcsc.com/product-detail/C1850418.html | 1 | 1 | 1 | $12.88 | $12.88 | $23.31
MAX-7456eui+ (U3) | Source: Aliexpress |  | https://www.aliexpress.com/item/33005990891.html | 1 | 1 | 1 | $4.28 | $4.28 | $27.59
BL8072CLTR-3.3 (3.3V LDO) (U6) | 3.3V | SOT-223-3 | https://www.lcsc.com/product-detail/C843780.html | 1 | 1 | 5 | $0.99 | $0.99 | $28.58
SGM2212-3.3XKC3G/TR (IMU LDO) (U7) | 3.3V | SOT-223-3 | https://www.lcsc.com/product-detail/C3294699.html | 1 | 1 | 1 | $0.61 | $0.61 | $29.19
W25Q128JVSIQ TR (Flash) (U8) |  | SOIC-8-208mil | https://www.lcsc.com/product-detail/C97521.html | 1 | 1 | 1 | $2.32 | $2.32 | $31.51
TPS62173DSG (5V BEC) (U4, U5) | 5V | WSON-8-EP(2x2) | https://www.lcsc.com/product-detail/C181384.html | 2 | 2 | 1 | $0.93 | $1.86 | $33.37
BMP280 Baro (U10) |  | LGA-8(2x2.5) | https://www.lcsc.com/product-detail/C83291.html | 1 | 1 | 1 | $6.90 | $6.90 | $40.27
27MHz Crystal (Y1) | 27MHz | SMD3225-4P | https://www.lcsc.com/product-detail/C9008.html | 1 | 1 | 10 | $0.77 | $0.77 | $41.04
8MHz Crystal w/ Caps (Y2) | 8MHz | SMD3213-3P | https://www.lcsc.com/product-detail/C907975.html | 1 | 1 | 5 | $1.05 | $1.05 | $42.09
BEC Inductors (L1, L2) | 2.2uH | 0806 | https://www.lcsc.com/product-detail/C695610.html | 1 | 1 | 5 | $0.82 | $0.82 | $42.91
BOOT Button (SW2) |  | SMD,4x3mm | https://www.lcsc.com/product-detail/C720477.html | 1 | 1 | 10 | $0.54 | $0.54 | $43.45
Reverse Pol. Mosfet (Q1) |  | SOT-23 | https://www.lcsc.com/product-detail/C15127.html | 1 | 1 | 10 | $0.59 | $0.59 | $44.04
USB Micro B Conn (J6) |  | SMD | https://www.lcsc.com/product-detail/C404969.html | 1 | 1 | 10 | $0.41 | $0.41 | $44.45

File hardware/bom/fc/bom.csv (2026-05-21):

Basic? | Desc | Value | Part Details | Package | JLCPCB | Num | Needed | Unit Price | Net Price | Running Total
CAPACITORS
TRUE | Baro Bypass Caps (C1, C2) | 100nF | 100nF 16V X7R ±10% 0402 Multilayer Ceramic Capacitors MLCC - SMD/SMT ROHS | 0402 | https://jlcpcb.com/partdetail/1877-CL05B104KO5NNNC/C1525 | 2 | 2 | $0.0013 | $0.00 | $0.00
TRUE | OSD Bypass Caps (C6,C7,C8) | 100nF | 100nF 16V X7R ±10% 0402 Multilayer Ceramic Capacitors MLCC - SMD/SMT ROHS | 0402 | https://jlcpcb.com/partdetail/1877-CL05B104KO5NNNC/C1525 | 3 | 3 | $0.0013 | $0.00 | $0.01
FALSE | OSD Filter Electrolytic Caps (C4, C5) | 47uF | -40?~+105? 1.5mm 1000hrs@105? 10V 47uF 4mm 5mm ±20% ??,D4xL5mm Aluminum Electrolytic Capacitors - Leaded ROHS | Plugin,D4xL5mm | https://jlcpcb.com/partdetail/44303-KF476M010C05RR0VH2FP0/C43312 | 2 | 0 | $0.0079 | $0.00 | $0.01
TRUE | OSD Filter Caps (C9) | 100nF | 100nF 16V X7R ±10% 0402 Multilayer Ceramic Capacitors MLCC - SMD/SMT ROHS | 0402 | https://jlcpcb.com/partdetail/1877-CL05B104KO5NNNC/C1525 | 1 | 1 | $0.0013 | $0.00 | $0.01
TRUE | IMU Bypass Cap (C10) | 100nF | 100nF 16V X7R ±10% 0402 Multilayer Ceramic Capacitors MLCC - SMD/SMT ROHS | 0402 | https://jlcpcb.com/partdetail/1877-CL05B104KO5NNNC/C1525 | 1 | 1 | $0.0013 | $0.00 | $0.01
TRUE | IMU Bypass Cap (C11) | 2.2uF | 2.2uF 6.3V X5R ±20% 0402 Multilayer Ceramic Capacitors MLCC - SMD/SMT ROHS | 0402 | https://jlcpcb.com/partdetail/13164-CL05A225MQ5NSNC/C12530 | 1 | 1 | $0.0028 | $0.00 | $0.01
TRUE | IMU Bypass Cap (C12) | 10nF | 10nF 50V X7R ±10% 0402 Multilayer Ceramic Capacitors MLCC - SMD/SMT ROHS | 0402 | https://jlcpcb.com/partdetail/15869-CL05B103KB5NNNC/C15195 | 1 | 1 | $0.0015 | $0.00 | $0.01
TRUE | 3.3V LDO Bypass Caps (C13,C14) | 1uF | 1uF 25V X5R ±10% 0402 Multilayer Ceramic Capacitors MLCC - SMD/SMT ROHS | 0402 | https://jlcpcb.com/partdetail/53938-CL05A105KA5NQNC/C52923 | 2 | 2 | $0.0041 | $0.01 | $0.02
TRUE | IMU LDO Bypass Caps (C15,C16) | 1uF | 1uF 25V X5R ±10% 0402 Multilayer Ceramic Capacitors MLCC - SMD/SMT ROHS | 0402 | https://jlcpcb.com/partdetail/53938-CL05A105KA5NQNC/C52923 | 2 | 2 | $0.0041 | $0.01 | $0.03
TRUE | IMU LDO Bypass Caps (C17,C18) | 22nF | 22nF 50V X7R ±10% 0402 Multilayer Ceramic Capacitors MLCC - SMD/SMT ROHS | 0402 | https://jlcpcb.com/partdetail/1884-0402B223K500NT/C1532 | 2 | 2 | $0.0019 | $0.00 | $0.03
TRUE | MCU Filter Caps (C19,C20) | 100nF | 100nF 16V X7R ±10% 0402 Multilayer Ceramic Capacitors MLCC - SMD/SMT ROHS | 0402 | https://jlcpcb.com/partdetail/1877-CL05B104KO5NNNC/C1525 | 1 | 1 | $0.0013 | $0.00 | $0.03
TRUE | Flash Filter Cap (C21) | 100nF | 100nF 16V X7R ±10% 0402 Multilayer Ceramic Capacitors MLCC - SMD/SMT ROHS | 0402 | https://jlcpcb.com/partdetail/1877-CL05B104KO5NNNC/C1525 | 1 | 1 | $0.0013 | $0.00 | $0.04
FALSE | 5V Bec Output Electrolytic Cap (C22) | 180uF | 10000hrs@105? 180uF 210m?@100kHz 3.5mm 35V 8mm 900mA@100kHz 9mm ±20% ??,D8xL9mm Aluminum Electrolytic Capacitors - Leaded ROHS | Plugin,D8xL9mm | https://jlcpcb.com/partdetail/Ymin-LKMD0901V181MF/C442870 | 1 | 0 | $0.0851 | $0.00 | $0.04
TRUE | 5V Bec Input Cap (C23) | 1uF | 1uF 25V X5R ±10% 0402 Multilayer Ceramic Capacitors MLCC - SMD/SMT ROHS | 0402 | https://jlcpcb.com/partdetail/53938-CL05A105KA5NQNC/C52923 | 1 | 1 | $0.0041 | $0.00 | $0.04
FALSE | 5V Bec Input Electrolytic Cap (C24) | 470uF | 10mm 16mm 35V 470uF 5mm 7000hrs@105? ±20% ??,D10xL16mm Aluminum Electrolytic Capacitors - Leaded ROHS | Plugin,D10xL16mm | https://jlcpcb.com/partdetail/AISHI_Aihua_Group-ERS1VM471G16OT/C106703 | 1 | 0 | $0.0732 | $0.00 | $0.04
FALSE | VTX Bec Output Electrolytic Cap (C27) | 180uF | 10000hrs@105? 180uF 210m?@100kHz 3.5mm 35V 8mm 900mA@100kHz 9mm ±20% ??,D8xL9mm Aluminum Electrolytic Capacitors - Leaded ROHS | Plugin,D8xL9mm | https://jlcpcb.com/partdetail/Ymin-LKMD0901V181MF/C442870 | 1 | 0 | $0.0851 | $0.00 | $0.04
TRUE | VTX Bec Input Cap (C26) | 1uF | 1uF 25V X5R ±10% 0402 Multilayer Ceramic Capacitors MLCC - SMD/SMT ROHS | 0402 | https://jlcpcb.com/partdetail/53938-CL05A105KA5NQNC/C52923 | 1 | 1 | $0.0041 | $0.00 | $0.04
FALSE | VTX Bec Input Electrolytic Cap (C25) | 470uF | 10mm 16mm 35V 470uF 5mm 7000hrs@105? ±20% ??,D10xL16mm Aluminum Electrolytic Capacitors - Leaded ROHS | Plugin,D10xL16mm | https://jlcpcb.com/partdetail/AISHI_Aihua_Group-ERS1VM471G16OT/C106703 | 1 | 0 | $0.0732 | $0.00 | $0.04
TRUE | MCU Filter Caps (C28, C29) | 2.2uF | 2.2uF 6.3V X5R ±20% 0402 Multilayer Ceramic Capacitors MLCC - SMD/SMT ROHS | 0402 | https://jlcpcb.com/partdetail/13164-CL05A225MQ5NSNC/C12530 | 2 | 2 | $0.0028 | $0.01 | $0.05
TRUE | VTX 10V BEC CFF Cap (C31) | 4.7uF | 16V 4.7uF X5R ±10% 0603 Multilayer Ceramic Capacitors MLCC - SMD/SMT ROHS | 0603 | https://jlcpcb.com/partdetail/20375-CL10A475KO8NNNC/C19666 | 1 | 1 | $0.0104 | $0.01 | $0.06
DIODES
FALSE | Blue LED (D1) |  | 100mW 120° 175mcd 3.1V 460nm~475nm 469nm 5mA Blue Discrete Diode Water Clear 0603 LED Indication - Discrete ROHS | 0603 | https://jlcpcb.com/partdetail/Hubei_KENTOElec-KT0603B/C2288 | 1 | 1 | $0.0101 | $0.01 | $0.07
FALSE | Green LED (D2) |  | -40?~+85? 10mA 130° 3.1V 517nm~527nm 66mW 780mcd Discrete Diode Green Water Clear 0603 LED Indication - Discrete ROHS | 0603 | https://jlcpcb.com/partdetail/23857064-PSC_1608U52GCG4/C22371297 | 1 | 1 | $0.0091 | $0.01 | $0.08
TRUE | Schottky Diode (D3, D4) |  | 1 Independent 1A 25A 40V 500uA@40V 600mV@1A SOD-323 Schottky Diodes ROHS | SOD-323 | https://jlcpcb.com/partdetail/GuangdongHottech-1N5819WS/C191023 | 2 | 2 | $0.0110 | $0.02 | $0.10
TRUE | BEC Schottky Diodes (D5, D6) |  | -55?~+125? 120A 40V 50uA@40V 550mV@5A 5A Independent SMA(DO-214AC) Schottky Diodes ROHS | SMA(DO-214AC) | https://jlcpcb.com/partdetail/hongjiacheng-SS54/C7420369 | 2 | 2 | $0.0442 | $0.09 | $0.19
RESISTORS
TRUE | OSD Imp. Res (R1) | 75? | -55?~+155? 50V 62.5mW 75? Thick Film Resistor ±1% ±100ppm/? 0402 Chip Resistor - Surface Mount ROHS | 0402 | https://jlcpcb.com/partdetail/25876-0402WGF750JTCE/C25133 | 1 | 1 | $0.0009 | $0.00 | $0.19
TRUE | Cam Pulldown (R2) | 75? | -55?~+155? 50V 62.5mW 75? Thick Film Resistor ±1% ±100ppm/? 0402 Chip Resistor - Surface Mount ROHS | 0402 | https://jlcpcb.com/partdetail/25876-0402WGF750JTCE/C25133 | 1 | 1 | $0.0009 | $0.00 | $0.19
TRUE | Volt Sense Div Res (R3) | 10k? | -55?~+155? 10k? 50V 62.5mW Thick Film Resistor ±1% ±100ppm/? 0402 Chip Resistor - Surface Mount ROHS | 0402 | https://jlcpcb.com/partdetail/26487-0402WGF1002TCE/C25744 | 1 | 1 | $0.0013 | $0.00 | $0.19
TRUE | Volt Sense Div Res (R4) | 100k? | -55?~+155? 100k? 50V 62.5mW Thick Film Resistor ±1% ±100ppm/? 0402 Chip Resistor - Surface Mount ROHS | 0402 | https://jlcpcb.com/partdetail/26484-0402WGF1003TCE/C25741 | 1 | 1 | $0.0009 | $0.00 | $0.19
TRUE | LED Current Lim Res (R5, R6) | 75? | -55?~+155? 50V 62.5mW 75? Thick Film Resistor ±1% ±100ppm/? 0402 Chip Resistor - Surface Mount ROHS | 0402 | https://jlcpcb.com/partdetail/25876-0402WGF750JTCE/C25133 | 2 | 2 | $0.0009 | $0.00 | $0.20
TRUE | USB Res (R7, R8) | 22? | -55?~+155? 22? 50V 62.5mW Thick Film Resistor ±1% ±100ppm/? 0402 Chip Resistor - Surface Mount ROHS | 0402 | https://jlcpcb.com/partdetail/25835-0402WGF220JTCE/C25092 | 2 | 2 | $0.0011 | $0.00 | $0.20
TRUE | Reverse Pol. Gate Res (R9) | 1k? | -55?~+155? 1k? 50V 62.5mW Thick Film Resistor ±1% ±100ppm/? 0402 Chip Resistor - Surface Mount ROHS | 0402 | https://jlcpcb.com/partdetail/12256-0402WGF1001TCE/C11702 | 1 | 1 | $0.0010 | $0.00 | $0.20
TRUE | VTX BEC Div Res (R10) | 1.8k? | -55?~+155? 1.8k? 100mW 75V Thick Film Resistor ±1% ±100ppm/? 0603 Chip Resistor - Surface Mount ROHS | 0603 | https://jlcpcb.com/partdetail/4584-0603WAF1801T5E/C4177 | 1 | 1 | $0.0015 | $0.00 | $0.20
TRUE | VTX BEC Div Res (R11) | 1.1k? | -55?~+155? 1.1k? 100mW 75V Thick Film Resistor ±1% ±100ppm/? 0603 Chip Resistor - Surface Mount ROHS | 0603 | https://jlcpcb.com/partdetail/23491-0603WAF1101T5E/C22764 | 1 | 1 | $0.0015 | $0.00 | $0.20
TRUE | I2C Pullup Res’s (R12, R13) | 2.2k? | -55?~+155? 2.2k? 50V 62.5mW Thick Film Resistor ±1% ±100ppm/? 0402 Chip Resistor - Surface Mount ROHS | 0402 | https://jlcpcb.com/partdetail/26622-0402WGF2201TCE/C25879 | 2 | 2 | $0.0009 | $0.00 | $0.20
TRUE | BOOT0 Pulldown Res (R14) | 10k? | -55?~+155? 10k? 50V 62.5mW Thick Film Resistor ±1% ±100ppm/? 0402 Chip Resistor - Surface Mount ROHS | 0402 | https://jlcpcb.com/partdetail/26487-0402WGF1002TCE/C25744 | 1 | 1 | $0.0013 | $0.00 | $0.21
JACKS
FALSE | Camera Conn (J1) | 3P SH | -40?~+85? 1 1A 1mm 1x3P 3 3.05mm 3P 4.4mm 5.35mm 50V Auxiliary Solder Pin Beige Brass LCP SH Surface Mount,Vertical Tin SMD,P=1mm Wire To Board Connector ROHS | SMD,P=1mm | https://jlcpcb.com/partdetail/Megastar-ZX_SH1_03PLT/C7430452 | 1 | 1 | $0.0680 | $0.07 | $0.27
FALSE | UART Conns (J2, J8, J9, J10) | 4P SH | -25?~+85? 1 1A 1mm 1x4P 3.76mm 4 4P 50V 6.3mm Beige Copper LCP SH Surface Mount,Vertical Tin SMD,P=1mm Wire To Board Connector ROHS | SMD,P=1mm | https://jlcpcb.com/partdetail/HongCheng-HCZZ00394/C7433440 | 4 | 4 | $0.0367 | $0.15 | $0.42
FALSE | VTX Conn (J4) | 5P SH | -25?~+85? 1 1A 1mm 1x5P 3.76mm 4.4mm 5 50V 5P 7.3mm Auxiliary Solder Pin LCP Phosphor bronze SH Surface Mount,Vertical Tin UL94V-0 SMD,P=1mm Wire To Board Connector ROHS | SMD,P=1mm | https://jlcpcb.com/partdetail/HCTL-HC_1_05PLT/C2845373 | 1 | 1 | $0.1148 | $0.11 | $0.53
TRUE | ESC Conn (J5) | 8P SH | -25?~+85? 1 10.3mm 1mm 1x8P 3.76mm 4.4mm 500mA 50V 8 8P LCP Phosphor bronze SH Surface Mount,Vertical Tin UL94V-0 SMD,P=1mm Wire To Board Connector ROHS | SMD,P=1mm | https://jlcpcb.com/partdetail/JUSHUO-AFC10_S08PCA00/C2764202 | 1 | 1 | $0.1222 | $0.12 | $0.66
OTHER
FALSE | STM32F405 (U1) |  | -40?~+85? 1.8V~3.6V 12bit 12bit 168MHz 192KB 1MB 32 Bit 51 ARM Cortex-M4 Built-in FLASH LQFP-64(10x10) Microcontrollers (MCU/MPU/SOC) ROHS | LQFP-64(10x10) | https://jlcpcb.com/partdetail/STMicroelectronics-STM32F405RGT6/C15742 | 1 | 1 | $4.7965 | $4.80 | $5.45
FALSE | ICM-42668-P : IMU (U2) |  | -40?~+85? 1.71V~3.6V 16bit 2KB 7.5uA IMU (accelerometer + gyroscope) SPI?I2C X,Y,Z X,Y,Z ±16g ±2000dps ????????????? LGA-14(2.5x3) Accelerometers ROHS | LGA-14(2.5x3) | https://jlcpcb.com/partdetail/TDKInvenSense-ICM_42688P/C1850418 | 1 | 1 | $11.2436 | $11.24 | $16.70
 | MAX-7456eui+ (U3) | Source: Aliexpress |  |  | https://www.aliexpress.com/item/33005990891.html | 1 | 1 | $4.47 | $4.47 | $21.17
FALSE | XL1509-ADJ (VTX 3.3V BEC) (U5) | 3.3V | -40?~+125? 1 1.23V~37V 150kHz 2A 2mA 4.5V~40V Adjustable Buck Buck Built-in No SOIC-8 DC-DC Converters ROHS | SOIC-8 | https://jlcpcb.com/partdetail/2773703-XL1509ADJ/C2681227 | 1 | 1 | $0.2421 | $0.24 | $21.41
FALSE | BL8072CLTR-3.3 (3.3V LDO) (U6) | 3.3V | -40?~+85?@(Ta) 1 18V 2A 3.3V 3uA 850mV@(1.5A) Fixed Positive SOT-223-3 Voltage Regulators - Linear, Low Drop Out (LDO) Regulators ROHS | SOT-223-3 | https://jlcpcb.com/partdetail/BL_Shanghai_Belling-BL8072CLTR33/C843780 | 1 | 1 | $0.1981 | $0.20 | $21.61
FALSE | SGM2212-3.3XKC3G/TR (IMU LDO) (U7) | 3.3V | -40?~+125? 0.002%Vout 20V 3.3V 450mV@(800mA) 800mA 80dB@(120Hz) 80uA Fixed Short Circuit Protection?Thermal Shutdown SOT-223-3 Voltage Regulators - Linear, Low Drop Out (LDO) Regulators ROHS | SOT-223-3 | https://jlcpcb.com/partdetail/SGMICRO-SGM2212_3_3XKC3GTR/C3294699 | 1 | 1 | $0.6068 | $0.61 | $22.21
TRUE | W25Q128JVSIQ TR (Flash) (U8) |  | -40?~+85? 100,000 cycles 120ms@(32KB) 128Mbit 133MHz 1uA 2.7V~3.6V 20 Years 3ms SPI SOIC-8-208mil NOR FLASH ROHS | SOIC-8-208mil | https://jlcpcb.com/partdetail/WinbondElec-W25Q128JVSIQ/C97521 | 1 | 1 | $1.9100 | $1.91 | $24.12
TRUE | XL1509-5.0 (5V BEC) (U9) | 5V | -40?~+85? 1 150kHz 2A 2mA 4.5V~40V 5V Buck Buck Built-in Fixed No SOIC-8 DC-DC Converters ROHS | SOIC-8 | https://jlcpcb.com/partdetail/XLSEMI-XL1509_50E1/C61063 | 1 | 1 | $0.2370 | $0.24 | $24.36
FALSE | BMP280 Baro (U10) |  | -40?~+85? 0.12hpa 1.5pa/K 1.71V~3.6V 1hpa 300nA 30Kpa~1.1bar I2C?SPI LGA-8(2x2.5) Pressure Sensors ROHS | LGA-8(2x2.5) | https://jlcpcb.com/partdetail/BoschSensortec-BMP280/C83291 | 1 | 1 | $6.2470 | $6.25 | $30.61
FALSE | 27MHz Crystal (Y1) | 27MHz | -40?~+85? 20pF 27MHz Crystal Oscillator ±10ppm ±20ppm SMD3225-4P Crystals ROHS | SMD3225-4P | https://jlcpcb.com/partdetail/YXC_CrystalOscillators-X322527MSB4SI/C9008 | 1 | 1 | $0.0764 | $0.08 | $30.68
FALSE | 8MHz Crystal w/ Caps (Y2) | 8MHz | -40?~+85? 10pF 40? 8MHz SMD3213-3P Ceramic Resonators ROHS | SMD3213-3P | https://jlcpcb.com/partdetail/973876-CSTNE8M00G520000R0/C907975 | 1 | 1 | $0.1909 | $0.19 | $30.88
FALSE | BEC Inductors (L1, L2) | 68uH | 1.8A 2A 315m? 68uH ±20% SMD,7.2x6.6mm Inductors (SMD) ROHS | SMD,7.2x6.6mm | https://jlcpcb.com/partdetail/SHOUHAN-CYA065068UH/C5189964 | 2 | 2 | $0.3052 | $0.61 | $31.49
TRUE | BOOT Button (SW2) |  | -30?~+80? 1.6N 100,000 cycles 12V 2mm 3mm 4mm 50mA Black Round Button SMD(SMT) Tab SPST Surface Mount,Vertical Without Bracket SMD,4x3mm Tactile Switches ROHS | SMD,4x3mm | https://jlcpcb.com/partdetail/XUNPU-TS_1088AR02016/C720477 | 1 | 1 | $0.0555 | $0.06 | $31.54
FALSE | VTX Channel Select (SW1) |  | 2.54mm 24V 25mA 3 Red SPST Slide, Rocked ??,P=2.54mm DIP Switches ROHS | Plugin,P=2.54mm | https://jlcpcb.com/partdetail/100634-DSWB03LHGET/C99420 | 1 | 1 | $0.2322 | $0.23 | $31.77
TRUE | Reverse Pol. Mosfet (Q1) |  | 1 P-Channel 14nC@10V 30V 47m?@10V?60m?@4.5V?85m?@2.5V 4A 55pF 645pF 80pF 900mV SOT-23 MOSFETs ROHS | SOT-23 | https://jlcpcb.com/partdetail/Alpha_OmegaSemicon-AO3401A/C15127 | 1 | 1 | $0.0584 | $0.06 | $31.83
FALSE | 5A Resettable Fuse | 5A | -40?~+85? 1.2A 12s 250V 2? 3.2W 5A 600mA 600m? ??,P=5.1mm Resettable Fuses ROHS | Plugin,P=5.1mm | https://jlcpcb.com/partdetail/343048-JK250600U/C369135 | 1 | 1 | $0.1795 | $0.18 | $32.01
FALSE | USB Micro B Conn (J6) |  | -20?~+85? 1 1.8A 30V 5,000 times 5P Black Female Micro-B Surface Mount, Right Angle USB 2.0 SMD USB Connectors ROHS | SMD | https://jlcpcb.com/partdetail/SHOUHAN-MicroXNJ/C404969 | 1 | 1 | $0.0402 | $0.04 | $32.05
TOTALS
 |  |  |  |  |  |  |  |  | Total: | $32.05

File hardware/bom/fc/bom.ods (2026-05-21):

Basic? | Desc | Value | Part Details | Package | JLCPCB | Num | Needed | Unit Price | Net Price | Running Total
CAPACITORS
TRUE | Baro Bypass Caps (C1, C2) | 100nF | 100nF 16V X7R ±10% 0402 Multilayer Ceramic Capacitors MLCC - SMD/SMT ROHS | 0402 | https://jlcpcb.com/partdetail/1877-CL05B104KO5NNNC/C1525 | 2 | 2 | $0.0013 | $0.00 | $0.00
TRUE | OSD Bypass Caps (C6,C7,C8) | 100nF | 100nF 16V X7R ±10% 0402 Multilayer Ceramic Capacitors MLCC - SMD/SMT ROHS | 0402 | https://jlcpcb.com/partdetail/1877-CL05B104KO5NNNC/C1525 | 3 | 3 | $0.0013 | $0.00 | $0.01
FALSE | OSD Filter Electrolytic Caps (C4, C5) | 47uF | -55℃~+105℃ 2000hrs@105℃ 47uF 4mm 5.4mm 6.3V ±20% SMD,D4xL5.4mm Aluminum Electrolytic Capacitors - SMD ROHS | SMD,D4xL5.4mm | https://jlcpcb.com/partdetail/HonorElec-RVT0J470M0405/C87853 | 2 | 0 | $0.0280 | $0.00 | $0.01
TRUE | OSD Filter Caps (C9) | 100nF | 100nF 16V X7R ±10% 0402 Multilayer Ceramic Capacitors MLCC - SMD/SMT ROHS | 0402 | https://jlcpcb.com/partdetail/1877-CL05B104KO5NNNC/C1525 | 1 | 1 | $0.0013 | $0.00 | $0.01
TRUE | IMU Bypass Cap (C10) | 100nF | 100nF 16V X7R ±10% 0402 Multilayer Ceramic Capacitors MLCC - SMD/SMT ROHS | 0402 | https://jlcpcb.com/partdetail/1877-CL05B104KO5NNNC/C1525 | 1 | 1 | $0.0013 | $0.00 | $0.01
TRUE | IMU Bypass Cap (C11) | 2.2uF | 2.2uF 6.3V X5R ±20% 0402 Multilayer Ceramic Capacitors MLCC - SMD/SMT ROHS | 0402 | https://jlcpcb.com/partdetail/13164-CL05A225MQ5NSNC/C12530 | 1 | 1 | $0.0028 | $0.00 | $0.01
TRUE | IMU Bypass Cap (C12) | 10nF | 10nF 50V X7R ±10% 0402 Multilayer Ceramic Capacitors MLCC - SMD/SMT ROHS | 0402 | https://jlcpcb.com/partdetail/15869-CL05B103KB5NNNC/C15195 | 1 | 1 | $0.0015 | $0.00 | $0.01
TRUE | 3.3V LDO Bypass Caps (C13,C14) | 1uF | 1uF 25V X5R ±10% 0402 Multilayer Ceramic Capacitors MLCC - SMD/SMT ROHS | 0402 | https://jlcpcb.com/partdetail/53938-CL05A105KA5NQNC/C52923 | 2 | 2 | $0.0041 | $0.01 | $0.02
TRUE | IMU LDO Bypass Caps (C15,C16) | 1uF | 1uF 25V X5R ±10% 0402 Multilayer Ceramic Capacitors MLCC - SMD/SMT ROHS | 0402 | https://jlcpcb.com/partdetail/53938-CL05A105KA5NQNC/C52923 | 2 | 2 | $0.0041 | $0.01 | $0.03
TRUE | IMU LDO Bypass Caps (C17,C18) | 22nF | 22nF 50V X7R ±10% 0402 Multilayer Ceramic Capacitors MLCC - SMD/SMT ROHS | 0402 | https://jlcpcb.com/partdetail/1884-0402B223K500NT/C1532 | 2 | 2 | $0.0019 | $0.00 | $0.03
TRUE | MCU Filter Caps (C19,C20) | 100nF | 100nF 16V X7R ±10% 0402 Multilayer Ceramic Capacitors MLCC - SMD/SMT ROHS | 0402 | https://jlcpcb.com/partdetail/1877-CL05B104KO5NNNC/C1525 | 1 | 1 | $0.0013 | $0.00 | $0.03
TRUE | Flash Filter Cap (C21) | 100nF | 100nF 16V X7R ±10% 0402 Multilayer Ceramic Capacitors MLCC - SMD/SMT ROHS | 0402 | https://jlcpcb.com/partdetail/1877-CL05B104KO5NNNC/C1525 | 1 | 1 | $0.0013 | $0.00 | $0.04
TRUE | MCU Filter Caps (C28, C29) | 2.2uF | 2.2uF 6.3V X5R ±20% 0402 Multilayer Ceramic Capacitors MLCC - SMD/SMT ROHS | 0402 | https://jlcpcb.com/partdetail/13164-CL05A225MQ5NSNC/C12530 | 2 | 2 | $0.0028 | $0.01 | $0.04
FALSE | BEC Output Electrolytic Caps (C27, C30) | 22uF | -40℃~+105℃ 10V 2000hrs@105℃ 22uF 4mm 5.4mm 60mA@120Hz ±20% SMD,D4xL5.4mm Aluminum Electrolytic Capacitors - SMD ROHS | SMD,D4xL5.4mm | https://jlcpcb.com/partdetail/ROQANG-RVT1A220M0405/C335975 | 2 | 2 | $0.0267 | $0.05 | $0.10
TRUE | MCU Filter Caps (C3, C22-C26) | 100nF | 100nF 16V X7R ±10% 0402 Multilayer Ceramic Capacitors MLCC - SMD/SMT ROHS | 0402 | https://jlcpcb.com/partdetail/1877-CL05B104KO5NNNC/C1525 | 1 | 1 | $0.0013 | $0.00 | $0.10
DIODES
FALSE | Blue LED (D1) |  | 100mW 120° 175mcd 3.1V 460nm~475nm 469nm 5mA Blue Discrete Diode Water Clear 0603 LED Indication - Discrete ROHS | 0603 | https://jlcpcb.com/partdetail/Hubei_KENTOElec-KT0603B/C2288 | 1 | 1 | $0.0101 | $0.01 | $0.11
FALSE | Green LED (D2) |  | -40℃~+85℃ 10mA 130° 3.1V 517nm~527nm 66mW 780mcd Discrete Diode Green Water Clear 0603 LED Indication - Discrete ROHS | 0603 | https://jlcpcb.com/partdetail/23857064-PSC_1608U52GCG4/C22371297 | 1 | 1 | $0.0091 | $0.01 | $0.12
TRUE | Schottky Diode (D3, D4) |  | 1 Independent 1A 25A 40V 500uA@40V 600mV@1A SOD-323 Schottky Diodes ROHS | SOD-323 | https://jlcpcb.com/partdetail/GuangdongHottech-1N5819WS/C191023 | 2 | 2 | $0.0110 | $0.02 | $0.14
TRUE | BEC Schottky Diodes (D5, D6) |  | -55℃~+125℃ 120A 40V 50uA@40V 550mV@5A 5A Independent SMA(DO-214AC) Schottky Diodes ROHS | SMA(DO-214AC) | https://jlcpcb.com/partdetail/hongjiacheng-SS54/C7420369 | 2 | 2 | $0.0442 | $0.09 | $0.23
RESISTORS
TRUE | OSD Imp. Res (R1) | 75Ω | -55℃~+155℃ 50V 62.5mW 75Ω Thick Film Resistor ±1% ±100ppm/℃ 0402 Chip Resistor - Surface Mount ROHS | 0402 | https://jlcpcb.com/partdetail/25876-0402WGF750JTCE/C25133 | 1 | 1 | $0.0009 | $0.00 | $0.23
TRUE | Cam Pulldown (R2) | 75Ω | -55℃~+155℃ 50V 62.5mW 75Ω Thick Film Resistor ±1% ±100ppm/℃ 0402 Chip Resistor - Surface Mount ROHS | 0402 | https://jlcpcb.com/partdetail/25876-0402WGF750JTCE/C25133 | 1 | 1 | $0.0009 | $0.00 | $0.23
TRUE | Volt Sense Div Res (R3) | 10kΩ | -55℃~+155℃ 10kΩ 50V 62.5mW Thick Film Resistor ±1% ±100ppm/℃ 0402 Chip Resistor - Surface Mount ROHS | 0402 | https://jlcpcb.com/partdetail/26487-0402WGF1002TCE/C25744 | 1 | 1 | $0.0013 | $0.00 | $0.23
TRUE | Volt Sense Div Res (R4) | 100kΩ | -55℃~+155℃ 100kΩ 50V 62.5mW Thick Film Resistor ±1% ±100ppm/℃ 0402 Chip Resistor - Surface Mount ROHS | 0402 | https://jlcpcb.com/partdetail/26484-0402WGF1003TCE/C25741 | 1 | 1 | $0.0009 | $0.00 | $0.23
TRUE | LED Current Lim Res (R5, R6) | 75Ω | -55℃~+155℃ 50V 62.5mW 75Ω Thick Film Resistor ±1% ±100ppm/℃ 0402 Chip Resistor - Surface Mount ROHS | 0402 | https://jlcpcb.com/partdetail/25876-0402WGF750JTCE/C25133 | 2 | 2 | $0.0009 | $0.00 | $0.23
TRUE | USB Res (R7, R8) | 22Ω | -55℃~+155℃ 22Ω 50V 62.5mW Thick Film Resistor ±1% ±100ppm/℃ 0402 Chip Resistor - Surface Mount ROHS | 0402 | https://jlcpcb.com/partdetail/25835-0402WGF220JTCE/C25092 | 2 | 2 | $0.0011 | $0.00 | $0.23
TRUE | Reverse Pol. Gate Res (R9) | 1kΩ | -55℃~+155℃ 1kΩ 50V 62.5mW Thick Film Resistor ±1% ±100ppm/℃ 0402 Chip Resistor - Surface Mount ROHS | 0402 | https://jlcpcb.com/partdetail/12256-0402WGF1001TCE/C11702 | 1 | 1 | $0.0010 | $0.00 | $0.24
TRUE | I2C Pullup Res’s (R12, R13) | 2.2kΩ | -55℃~+155℃ 2.2kΩ 50V 62.5mW Thick Film Resistor ±1% ±100ppm/℃ 0402 Chip Resistor - Surface Mount ROHS | 0402 | https://jlcpcb.com/partdetail/26622-0402WGF2201TCE/C25879 | 2 | 2 | $0.0009 | $0.00 | $0.24
TRUE | BOOT0 Pulldown Res (R14) | 10kΩ | -55℃~+155℃ 10kΩ 50V 62.5mW Thick Film Resistor ±1% ±100ppm/℃ 0402 Chip Resistor - Surface Mount ROHS | 0402 | https://jlcpcb.com/partdetail/26487-0402WGF1002TCE/C25744 | 1 | 1 | $0.0013 | $0.00 | $0.24
TRUE | 5V BEC Res (R11, R15) | 100kΩ | -55℃~+155℃ 100kΩ 50V 62.5mW Thick Film Resistor ±1% ±100ppm/℃ 0402 Chip Resistor - Surface Mount ROHS | 0402 | https://jlcpcb.com/partdetail/26484-0402WGF1003TCE/C25741 | 1 | 1 | $0.0009 | $0.00 | $0.24
JACKS
FALSE | Camera Conn (J1) | 3P SH | -40℃~+85℃ 1 1A 1mm 1x3P 3 3.05mm 3P 4.4mm 5.35mm 50V Auxiliary Solder Pin Beige Brass LCP SH Surface Mount,Vertical Tin SMD,P=1mm Wire To Board Connector ROHS | SMD,P=1mm | https://jlcpcb.com/partdetail/Megastar-ZX_SH1_03PLT/C7430452 | 1 | 1 | $0.0680 | $0.07 | $0.31
FALSE | UART Conns (J2, J8, J9, J10) | 4P SH | -25℃~+85℃ 1 1A 1mm 1x4P 3.76mm 4 4P 50V 6.3mm Beige Copper LCP SH Surface Mount,Vertical Tin SMD,P=1mm Wire To Board Connector ROHS | SMD,P=1mm | https://jlcpcb.com/partdetail/HongCheng-HCZZ00394/C7433440 | 4 | 4 | $0.0367 | $0.15 | $0.45
FALSE | VTX Conn (J4) | 5P SH | -25℃~+85℃ 1 1A 1mm 1x5P 3.76mm 4.4mm 5 50V 5P 7.3mm Auxiliary Solder Pin LCP Phosphor bronze SH Surface Mount,Vertical Tin UL94V-0 SMD,P=1mm Wire To Board Connector ROHS | SMD,P=1mm | https://jlcpcb.com/partdetail/HCTL-HC_1_05PLT/C2845373 | 1 | 1 | $0.1148 | $0.11 | $0.57
TRUE | ESC Conn (J5) | 8P SH | -25℃~+85℃ 1 10.3mm 1mm 1x8P 3.76mm 4.4mm 500mA 50V 8 8P LCP Phosphor bronze SH Surface Mount,Vertical Tin UL94V-0 SMD,P=1mm Wire To Board Connector ROHS | SMD,P=1mm | https://jlcpcb.com/partdetail/JUSHUO-AFC10_S08PCA00/C2764202 | 1 | 1 | $0.1222 | $0.12 | $0.69
OTHER
FALSE | STM32F405 (U1) |  | -40℃~+85℃ 1.8V~3.6V 12bit 12bit 168MHz 192KB 1MB 32 Bit 51 ARM Cortex-M4 Built-in FLASH LQFP-64(10x10) Microcontrollers (MCU/MPU/SOC) ROHS | LQFP-64(10x10) | https://jlcpcb.com/partdetail/STMicroelectronics-STM32F405RGT6/C15742 | 1 | 1 | $4.7965 | $4.80 | $5.49
FALSE | ICM-42668-P : IMU (U2) |  | -40℃~+85℃ 1.71V~3.6V 16bit 2KB 7.5uA IMU (accelerometer + gyroscope) SPI、I2C X,Y,Z X,Y,Z ±16g ±2000dps 运动事件检测、同步与时间戳 LGA-14(2.5x3) Accelerometers ROHS | LGA-14(2.5x3) | https://jlcpcb.com/partdetail/TDKInvenSense-ICM_42688P/C1850418 | 1 | 1 | $11.2436 | $11.24 | $16.73
 | MAX-7456eui+ (U3) | Source: Aliexpress |  |  | https://www.aliexpress.com/item/33005990891.html | 1 | 1 | $4.47 | $4.47 | $21.20
FALSE | BL8072CLTR-3.3 (3.3V LDO) (U6) | 3.3V | -40℃~+85℃@(Ta) 1 18V 2A 3.3V 3uA 850mV@(1.5A) Fixed Positive SOT-223-3 Voltage Regulators - Linear, Low Drop Out (LDO) Regulators ROHS | SOT-223-3 | https://jlcpcb.com/partdetail/BL_Shanghai_Belling-BL8072CLTR33/C843780 | 1 | 1 | $0.1981 | $0.20 | $21.40
FALSE | SGM2212-3.3XKC3G/TR (IMU LDO) (U7) | 3.3V | -40℃~+125℃ 0.002%Vout 20V 3.3V 450mV@(800mA) 800mA 80dB@(120Hz) 80uA Fixed Short Circuit Protection、Thermal Shutdown SOT-223-3 Voltage Regulators - Linear, Low Drop Out (LDO) Regulators ROHS | SOT-223-3 | https://jlcpcb.com/partdetail/SGMICRO-SGM2212_3_3XKC3GTR/C3294699 | 1 | 1 | $0.6068 | $0.61 | $22.01
TRUE | W25Q128JVSIQ TR (Flash) (U8) |  | -40℃~+85℃ 100,000 cycles 120ms@(32KB) 128Mbit 133MHz 1uA 2.7V~3.6V 20 Years 3ms SPI SOIC-8-208mil NOR FLASH ROHS | SOIC-8-208mil | https://jlcpcb.com/partdetail/WinbondElec-W25Q128JVSIQ/C97521 | 1 | 1 | $1.9100 | $1.91 | $23.92
TRUE | TPS62173DSG (5V BEC) (U4, U5) | 5V | -40℃~+125℃@(TJ) 1 17uA 2.25MHz 3V~17V 500mA 5V Buck Buck Built-in Fixed Yes WSON-8-EP(2x2) DC-DC Converters ROHS | WSON-8-EP(2x2) | https://jlcpcb.com/partdetail/TexasInstruments-TPS62173DSGR/C181384 | 2 | 2 | $0.6629 | $1.33 | $25.24
FALSE | BMP280 Baro (U10) |  | -40℃~+85℃ 0.12hpa 1.5pa/K 1.71V~3.6V 1hpa 300nA 30Kpa~1.1bar I2C、SPI LGA-8(2x2.5) Pressure Sensors ROHS | LGA-8(2x2.5) | https://jlcpcb.com/partdetail/BoschSensortec-BMP280/C83291 | 1 | 1 | $6.2470 | $6.25 | $31.49
FALSE | 27MHz Crystal (Y1) | 27MHz | -40℃~+85℃ 20pF 27MHz Crystal Oscillator ±10ppm ±20ppm SMD3225-4P Crystals ROHS | SMD3225-4P | https://jlcpcb.com/partdetail/YXC_CrystalOscillators-X322527MSB4SI/C9008 | 1 | 1 | $0.0764 | $0.08 | $31.57
FALSE | 8MHz Crystal w/ Caps (Y2) | 8MHz | -40℃~+85℃ 10pF 40Ω 8MHz SMD3213-3P Ceramic Resonators ROHS | SMD3213-3P | https://jlcpcb.com/partdetail/973876-CSTNE8M00G520000R0/C907975 | 1 | 1 | $0.1909 | $0.19 | $31.76
FALSE | BEC Inductors (L1, L2) | 2.2uH | 1.9A 130mΩ 2.2uH 2.6A Thin-Film Inductor ±20% 0806 Inductors (SMD) ROHS | 0806 | https://jlcpcb.com/partdetail/TDK-TFM201610ALM2R2MTAA/C695610 | 1 | 1 | $0.1650 | $0.17 | $31.92
TRUE | BOOT Button (SW2) |  | -30℃~+80℃ 1.6N 100,000 cycles 12V 2mm 3mm 4mm 50mA Black Round Button SMD(SMT) Tab SPST Surface Mount,Vertical Without Bracket SMD,4x3mm Tactile Switches ROHS | SMD,4x3mm | https://jlcpcb.com/partdetail/XUNPU-TS_1088AR02016/C720477 | 1 | 1 | $0.0555 | $0.06 | $31.98
FALSE | VTX Channel Select (SW1) |  | 2.54mm 24V 25mA 3 Red SPST Slide, Rocked 插件,P=2.54mm DIP Switches ROHS | Plugin,P=2.54mm | https://jlcpcb.com/partdetail/100634-DSWB03LHGET/C99420 | 1 | 1 | $0.2322 | $0.23 | $32.21
TRUE | Reverse Pol. Mosfet (Q1) |  | 1 P-Channel 14nC@10V 30V 47mΩ@10V、60mΩ@4.5V、85mΩ@2.5V 4A 55pF 645pF 80pF 900mV SOT-23 MOSFETs ROHS | SOT-23 | https://jlcpcb.com/partdetail/Alpha_OmegaSemicon-AO3401A/C15127 | 1 | 1 | $0.0584 | $0.06 | $32.27
FALSE | 5A Resettable Fuse | 5A | -40℃~+85℃ 1.2A 12s 250V 2Ω 3.2W 5A 600mA 600mΩ 插件,P=5.1mm Resettable Fuses ROHS | Plugin,P=5.1mm | https://jlcpcb.com/partdetail/343048-JK250600U/C369135 | 1 | 1 | $0.1795 | $0.18 | $32.45
FALSE | USB Micro B Conn (J6) |  | -20℃~+85℃ 1 1.8A 30V 5,000 times 5P Black Female Micro-B Surface Mount, Right Angle USB 2.0 SMD USB Connectors ROHS | SMD | https://jlcpcb.com/partdetail/SHOUHAN-MicroXNJ/C404969 | 1 | 1 | $0.0402 | $0.04 | $32.49
TOTALS
 |  |  |  |  |  |  |  |  | Total: | $32.49

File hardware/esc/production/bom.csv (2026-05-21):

Designator | Footprint | Quantity | Value | LCSC Part #
C1, C15, C17, C2, C25, C26, C27, C28, C29, C3, C31, C39, C4, C40, C41, C42, C43, C45, C5, C53, C54, C55, C56, C57, C58, C6, C61, C62 | 0402 | 28 | 100nF
C10, C11, C7, C9 | 0603 | 4 | 22uF
C18, C33, C46, C8 | 0603 | 4 | 4.7uF
C59, C63 | 0805 | 2 | 22uF
D4 | 0603 | 1 | LED
J1 | JST_SH_BM08B-SRSS-TB_1x08-1MP_P1.00mm_Vertical | 1 | JST SH 1.0mm
L1 | 0603 | 1 | XRIM160808SR47MBCD
Q1, Q10, Q11, Q12, Q13, Q14, Q15, Q16, Q17, Q18, Q19, Q2, Q20, Q21, Q22, Q23, Q24, Q3, Q4, Q5, Q6, Q7, Q8, Q9 | POWERPAK-1212-8_L3.0-W3.0-P0.65-LS3.3-BL | 24 | Q_NMOS
R1, R2, R27, R28, R3, R32, R33, R37, R38, R4, R47, R48, R5, R52, R53, R57, R58, R6, R67, R68, R72, R73, R77, R78 | 0402 | 24 | 22R
R10, R15, R18, R19, R22, R9 | RES_4D03_0603_3P2X1P6_ROH | 6 | ~
R11, R13, R16, R26, R29, R30, R31, R34, R35, R36, R39, R40, R46, R49, R66, R8 | 0402 | 16 | 1k
R21 | BVNZR000510 | 1 | 0.5m
R25, R43, R45, R65, R7, R83 | 0402 | 6 | 10k
R42 | 0402 | 1 | 100k
R64 | 0402 | 1 | 2.2k
R82 | 0603 | 1 | 124k
T1, T3, T6, T8 | TestPoint_Pad_D1.0mm | 4 | SWDIO
T2, T4, T5, T7 | TestPoint_Pad_D1.0mm | 4 | SWDCLK
U1, U5, U7, U9 | QFN-24_L4.0-W4.0-P0.50-TL-EP2.8 | 4 | NSG2065Q | C41414478
U10 | WSON-6_L2.0-W2.0-P0.65-TL-EP | 1 | TLV76733DRVR | C2848334
U11 | SOT-23-6_L2.9-W1.6-P0.95-LS2.9-BL | 1 | LMR51420YDDCR | C5383002
U2, U4, U6, U8 | QFN-28_L4.0-W4.0-P0.40-TL-EP2.4 | 4 | AT32F421G8U7 | C2765098
U3 | SOT-23-5 | 1 | INA180B2

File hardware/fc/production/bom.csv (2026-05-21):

Designator | Footprint | Quantity | Value | LCSC Part #
C1, C10, C19, C2, C20, C21, C22, C23, C24, C25, C26, C3, C6, C7, C8, C9 | 0402 | 16 | 100nF
C11, C28, C29 | 0402 | 3 | 2.2uF
C12 | 0402 | 1 | 10nF
C13, C14, C15, C16 | 0402 | 4 | 1uF
C17, C18 | 0402 | 2 | 22nF
C27, C30 | CP_Elec_4x5.4 | 2 | 22uF
C4, C5 | CP_Elec_4x5.4 | 2 | 47uF
D1, D2 | 0603 | 2 | LED
D3, D4 | D_SOD-323 | 2 | D_Schottky
J1 | JST_SH_BM03B-SRSS-TB_1x03-1MP_P1.00mm_Vertical | 1 | Camera
J2 | JST_SH_BM04B-SRSS-TB_1x04-1MP_P1.00mm_Vertical | 1 | ELRS
J3 | SolderWire-0.1sqmm_1x02_P3.6mm_D0.4mm_OD1mm | 1 | Buzzer
J4 | JST_SH_BM05B-SRSS-TB_1x05-1MP_P1.00mm_Vertical | 1 | VTX
J5 | JST_SH_BM08B-SRSS-TB_1x08-1MP_P1.00mm_Vertical | 1 | ESC
J6 | SHOUHAN_MICROXNJ | 1 | USB_B_Micro
J7 | SolderWire-0.1sqmm_1x02_P3.6mm_D0.4mm_OD1mm | 1 | Debug
J8 | JST_SH_BM04B-SRSS-TB_1x04-1MP_P1.00mm_Vertical | 1 | UART5
J9 | JST_SH_BM04B-SRSS-TB_1x04-1MP_P1.00mm_Vertical | 1 | UART4
L1, L2 | INDC1608X95N | 2 | 2.2uH/2A
Q1 | SOT-23 | 1 | Q_PMOS
R1, R2, R5, R6 | 0402 | 4 | 75
R11, R15, R4 | 0402 | 3 | 100k
R12, R13 | 0402 | 2 | 2.2K
R14, R3 | 0402 | 2 | 10k
R7, R8 | 0402 | 2 | 22
R9 | 0402 | 1 | 1k
SW2 | SW_TS-1088-AR02016 | 1 | SW_Push
T2 | TestPoint_Pad_D1.0mm | 1 | 5V Bec
T3 | TestPoint_Pad_D1.0mm | 1 | 3.3V IMU
T4 | TestPoint_Pad_D1.0mm | 1 | 3.3V
T6 | TestPoint_Pad_D1.0mm | 1 | 5V VTX
TP5 | TestPoint_Pad_D1.0mm | 1 | 4.5V
U1 | LQFP-64_10x10mm_P0.5mm | 1 | STM32F405RGTx
U10 | Bosch_LGA-8_2x2.5mm_P0.65mm_ClockwisePinNumbering | 1 | BMP280
U2 | PQFN50P300X250X97-14N | 1 | ICM-42688-P
U3 | 21-0108G_U28E-5_MXM | 1 | max7456eui+
U4, U5 | WSON-8-1EP_2x2mm_P0.5mm_EP0.9x1.6mm_ThermalVias | 2 | TPS62173DSG
U6 | SOT-223-3_TabPin2 | 1 | BL8072CLTR33
U7 | SOT-223-3_TabPin2 | 1 | SGM2212-3.3XKC3G/TR
U8 | SOIC_208MIL_WIN | 1 | W25Q128JVSIQ TR
Y1 | Crystal_SMD_3225-4Pin_3.2x2.5mm | 1 | 27MHz
Y2 | OSC_CSTNE8M00G520000R0 | 1 | CSTNE8M00G520000R0

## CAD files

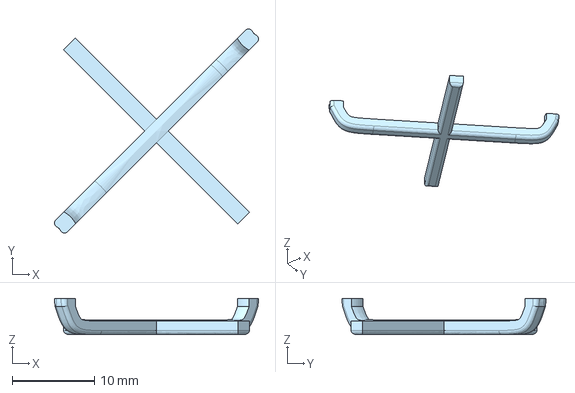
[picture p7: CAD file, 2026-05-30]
hardware/cad/battery-support.step
24.8 x 24.8 x 4.39 mm

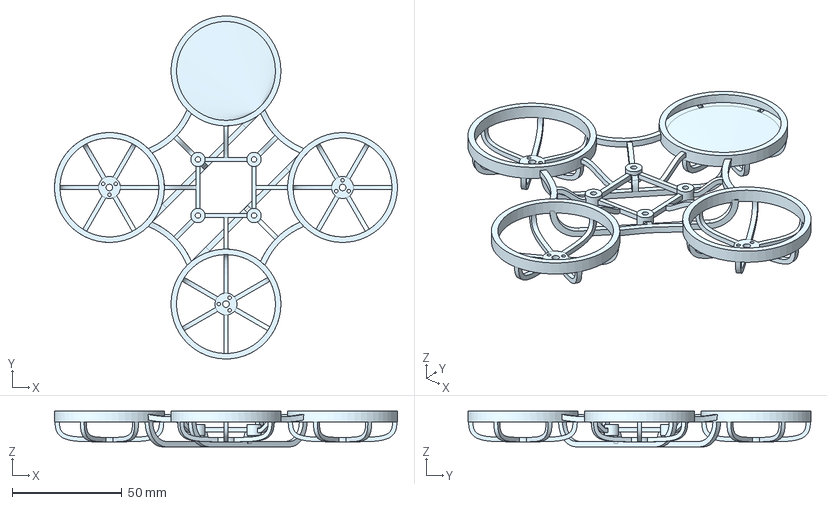
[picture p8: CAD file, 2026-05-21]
hardware/cad/sim/frame-simplified.step
156.1 x 156.1 x 16.2 mm

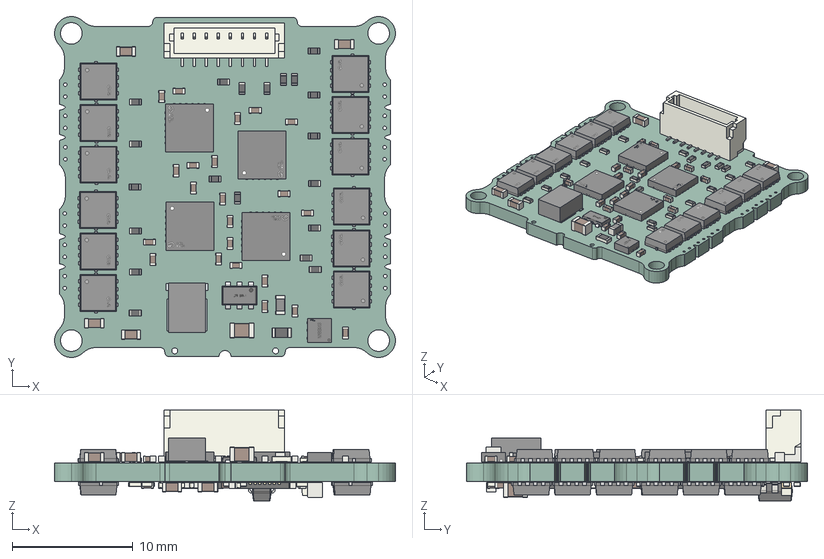
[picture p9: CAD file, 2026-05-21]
hardware/esc/esc.step
28.3 x 28.3 x 7.55 mm
WSON-6_L2.0-W2.0-H0.8-P0.65
C_0402_1005Metric x 28
R_0402_1005Metric x 48
POWERPAK-1212-8_L3.0-W3.0-P0.65-LS3.3-BL x 24
QFN-24_L4.0-W4.0-P0.50-TL-EP2.8 x 4
C_0603_1608Metric x 8
SOT-23-6_L2.9-W1.6-P0.95-LS2.9-BL
JST_SH_BM08B-SRSS-TB_1x08-1MP_P1.00mm_Vertical
Pins
L_0603_1608Metric
R_0603_1608Metric
C_0805_2012Metric x 2
SOT-23-5
R_Array_Convex_4x0603 x 6
LED_0603_1608Metric
UQFN-28_L4.0-W4.0-H0.5-P0.40-BL-EP2.4 x 4
esc_PCB

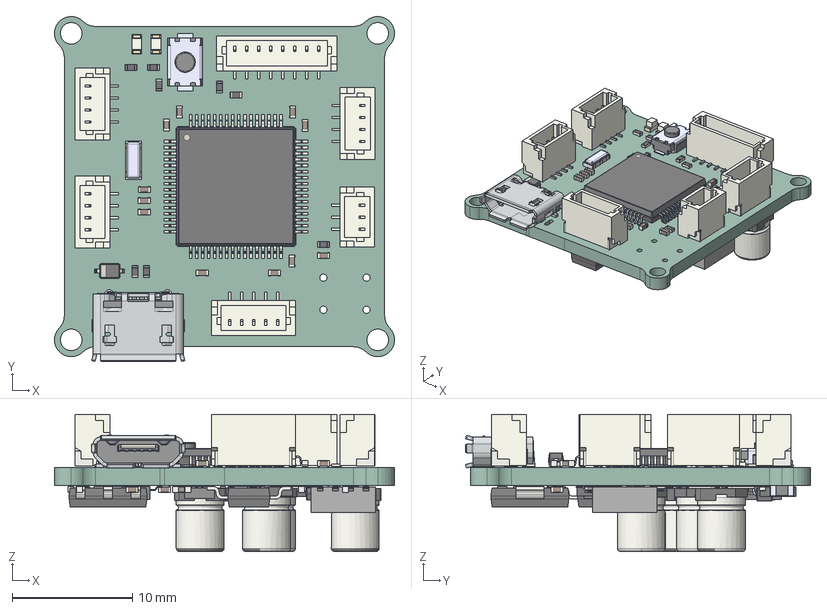
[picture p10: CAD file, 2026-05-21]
hardware/fc/fc.step
28.3 x 28.7 x 11.4 mm
R_0402_1005Metric x 14
JST_SH_BM04B-SRSS-TB_1x04-1MP_P1.00mm_Vertical x 3
C_0402_1005Metric x 26
TS-1088-AR02016
LED_0603_1608Metric x 2
D_SOD-323 x 2
CSTNE8M00G520000R0
shield
socket_housing
socket_plate
terminal x 5
JST_SH_BM08B-SRSS-TB_1x08-1MP_P1.00mm_Vertical
JST_SH_BM05B-SRSS-TB_1x05-1MP_P1.00mm_Vertical
LQFP-64_10x10mm_P0.5mm
JST_SH_BM03B-SRSS-TB_1x03-1MP_P1.00mm_Vertical
ASMPH-0806-1R0M-T x 2
CP_Elec_4x5.4 x 4
ICM-42688-P
SOIC_208MIL_WIN
WSON-8-1EP_2x2mm_P0.5mm_EP0.9x1.6mm x 2
Bosch_LGA-8_2x2.5mm_P0.65mm_ClockwisePinNumbering
Crystal_SMD_3225-4Pin_3.2x2.5mm
SOT-223 x 2
SOT-23
21-0108G_U28E-5_MXM
fc_PCB

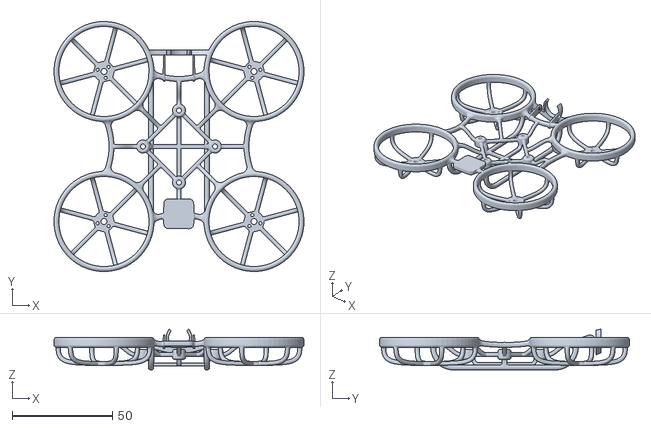
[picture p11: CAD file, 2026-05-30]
hardware/cad/frame-merged.stl
125.0 x 125.0 x 20.4

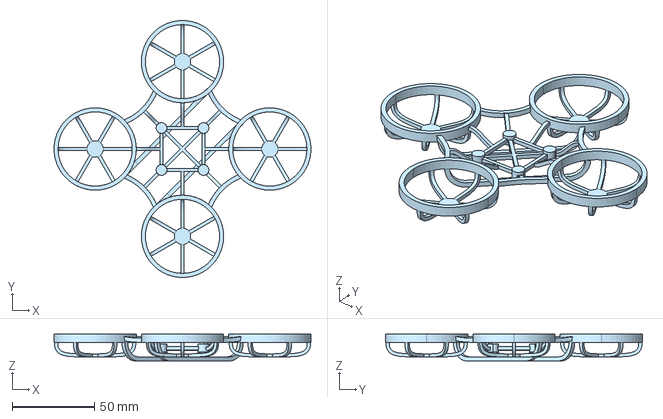
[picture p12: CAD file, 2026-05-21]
hardware/cad/sim/frame-center-brace.step
156.1 x 156.1 x 16.2 mm

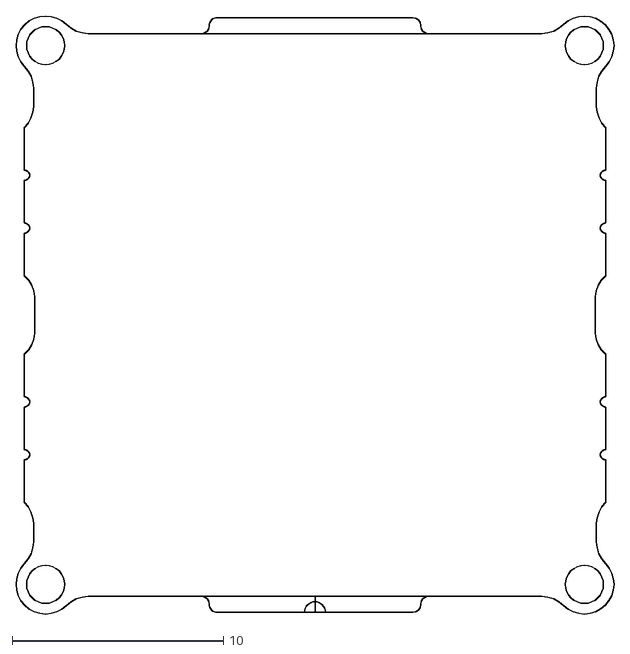
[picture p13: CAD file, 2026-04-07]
hardware/esc/BoardOutlineV2.dxf
28.3 x 28.3

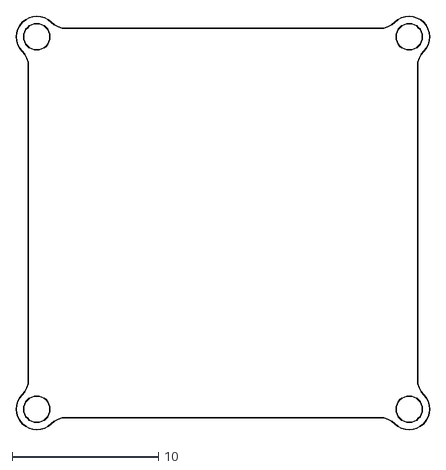
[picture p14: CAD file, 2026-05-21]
hardware/fc/board_outline.dxf
28.3 x 28.3

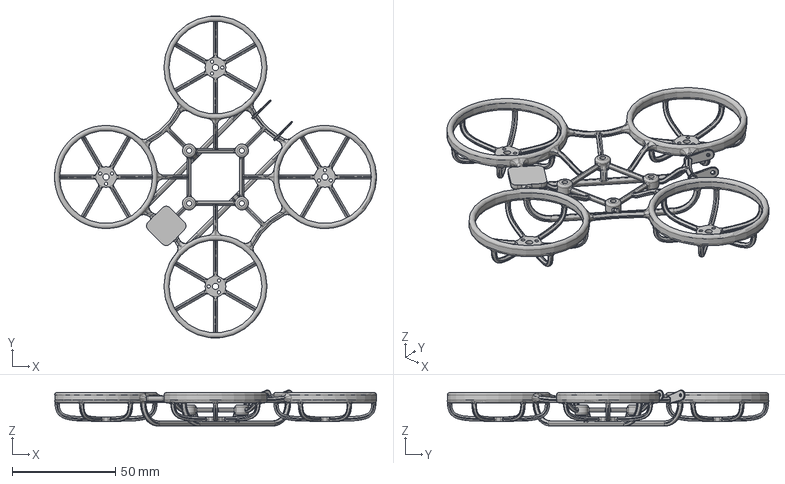
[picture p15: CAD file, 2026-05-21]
hardware/cad/frame.step
156.1 x 156.0 x 17.4 mm

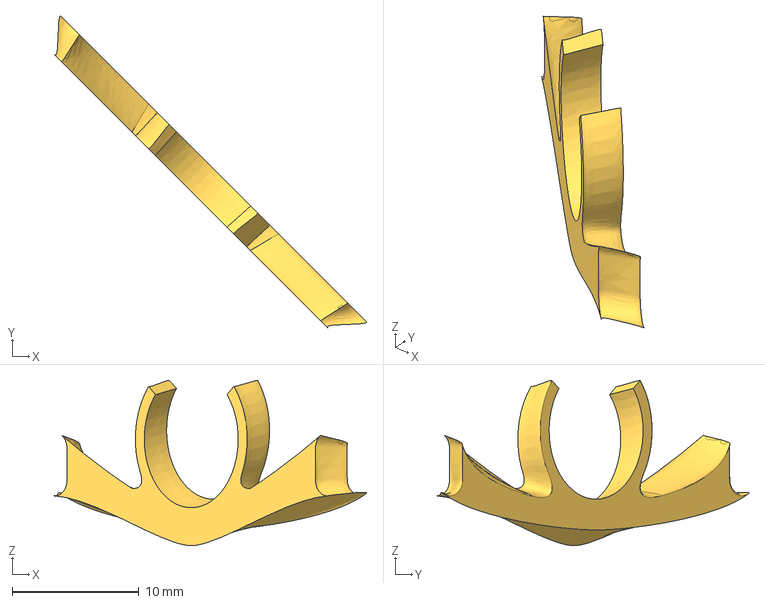
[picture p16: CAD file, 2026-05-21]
hardware/cad/camera-mount.step
24.7 x 24.7 x 13.1 mm

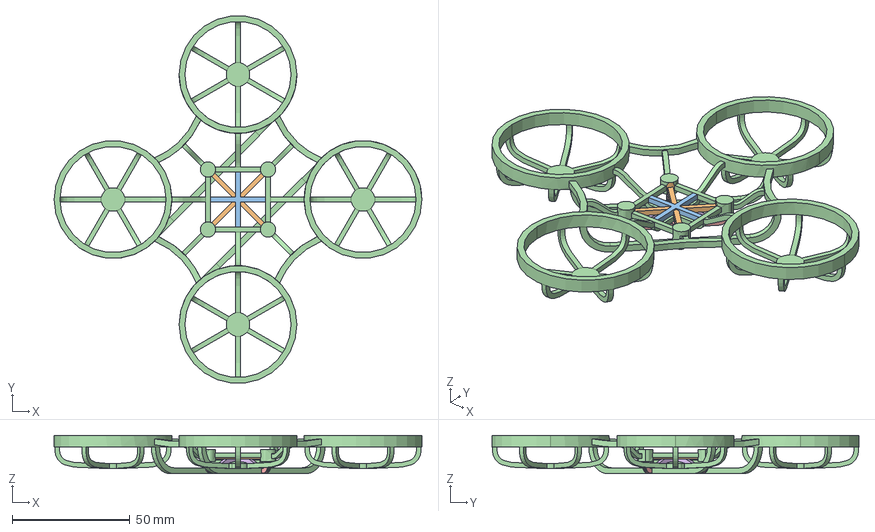
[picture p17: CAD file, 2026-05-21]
hardware/cad/sim/drone.FCStd
156.1 x 155.7 x 16.2 mm
Frame
Frame Center Brace
Frame Diagonal Brace
Frame Diagonal Support
Frame Straight Support
Frame Curved Support

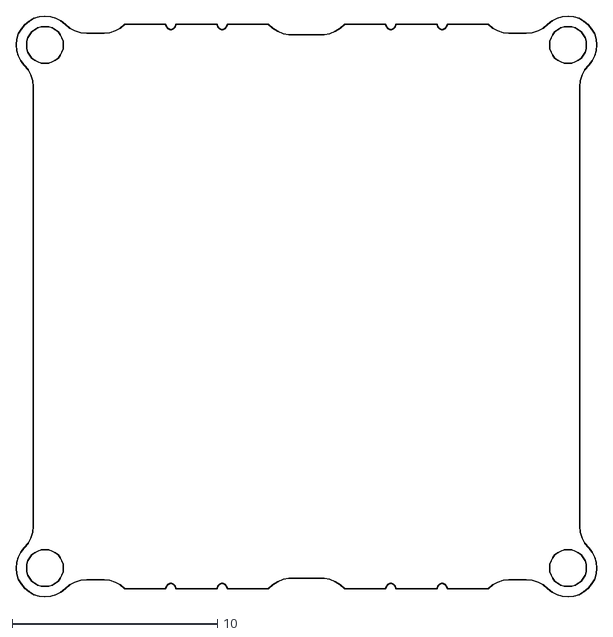
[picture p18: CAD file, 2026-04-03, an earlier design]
hardware/esc/BoardOutlineV1.dxf
28.3 x 28.3

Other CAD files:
hardware/cad/sim/frame-diagonal-bracing.step
hardware/cad/sim/frame-straight-support.step
hardware/cad/sim/frame diagonall-support.step
hardware/cad/sim/frame-cuved-supports.step
hardware/cad/battery-support.stl
hardware/cad/camera-mount.stl
hardware/cad/drone.blend
hardware/cad/frame.stl
hardware/cad/render/assets/materials/black-plastic_3be9fcbd-ee9a-446b-becc-2244dd5724cf/black-plastic_2K_b67ab6fb-b5e8-4cf3-b005-4679db24ad34.blend
hardware/cad/render/assets/materials/black-plastic_e872536a-48ed-4424-ac7b-80dc008e9748/black-plastic_2K_c94cf275-089d-43ee-92c3-5c641194570c.blend
hardware/cad/render/assets/materials/carpet-fabric_0e3d204f-234e-4f4e-9ff1-70ed337aece7/carpet-fabric_2K_9d336295-e381-46eb-88bb-80476ad84bde.blend
hardware/cad/render/assets/materials/dirty-white-plas_0c8cea32-5eae-4748-aadd-be4c20bbb916/dirty-white-plastic_2K_8bf06a50-b863-4997-bb8b-07ee627d3145.blend
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

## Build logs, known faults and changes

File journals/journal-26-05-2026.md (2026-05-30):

# Drone Journal 36 - 26/05/2026

Welp this journal has been a bit in the making lol.
I've basically spent this last week (Up till the 30th) doing a crapton of gaming (bg3 my beloved) and kinda having a bit of a break from intense fallout work, but I've started getting back into it now. Throughout the week, I've been working on basically just a bunch of odd jobs, so I'll go through those now.

---

First up, I actually added the supports from the sim version to the actual frame. This took a minute because holy crap booleans suck in onshape but whatevs, just chuked it into blender and stuck them together there.

---

Next up, I actually added the cost of the frame onto my bom, and realised I had also forgot to include the boards (and the frame) in the totals section, so updated that as well. 

This took ages because jlc3dp refused to accept my files (parse error) but eventually I fixed it by just importing to cura and then exporting stl from cura, whatevs, just a wee bit annoying. 

Also figured out some stuff with JLCPCB pricing that was being super weird, turns out you can only have one 'special offer' item in your cart at once. My plan is just to either order the FC and ESC in two seperate orders if that works, but if not I can always just make another account or something (For legal purposes I do not intend to do this :), this was a joke).

Logged in vs Not logged in

---

Finally, I went and made up a wee wiring diagram for the whole thing, which I think looks rather snazzy:
Wiring diagram

Doesn't show all of the details but its well enough to get it working :)

And finally, today I went back over all the submission requirements, and now I'm ready to actually submit it :O

So yeah! Submitting now, wish me luck lol :)

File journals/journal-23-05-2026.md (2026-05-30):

# Drone Journal 34 - 23/05/2026

Been a day (bc I was extremely tired yesterday lol), but today I made some major progress!

Following the checklist from yesterday:
- [ ] Replace placeholder renders 
- [ ] Add BOM 
- [ ] Add Zine Page
- [ ] Replace main render with different color scheme

The first thing I worked on was the zine page, and as I mentioned earlier I'm using the gruvbox theme. For the layout, I wanted something more rigid than with the VCO zine, just for a bit of a different vibe and also to accentuate the kinda tf2-y aesthetics

Heres the initial layout:
Initial layout
It did take a minute to get the render fitting in right, blenders color space stuff was screwing with the colors and that was confusing lol.

Then filled in some text:
W/ text

And then a background and some final polish:
Polished

This one section took me ages but I think its a fun wee detail:
Tiny section w/ 3d looking thing

Then moved onto working on the other stuff, namely replacing the placeholder renders. I settled on one more which was just another angle of the drone without all the camera effects and stuff.

Render 3

And then finally I did a wee exploded view:
Exploded view

Annd thats about it, last thing left to do is the bom :( not really looking forward to it but whatever.

Also finally going to go and buy fudge tomorrow! I have enough for ~0.5 kg which is honestly a ridiculous amount of fudge.

Night journal reading person. If you are a reviewer I hope you have a wonderful day, you should get some yummy desert tonight :) you deserve it <3

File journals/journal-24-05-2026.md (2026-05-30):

# Drone Journal 35 - 24/05/2026

Today is BOM day!
Time to figure out how I'm actually going to make all this :O

Starting off with the esc cos why not!

## ESC

I originally made this bom with the intent of using pcba, but I think it's highly unlikely that will happen, so I'm gonna swap all the jlc links over to lcsc. I could use ali but I feel like its very likely to just be more expensive because of shipping (one of the many perks of living in nz lol).

---

A wee bit through and I've also got a bunch of duplicate components (I was organising them by purpose more rather than type) but I'd like to only have one entry for each, as it massively simplifies everything tbh. Not going to include part designators, you can just read the schematic :)

---

And after a bunch more work we now have a nice clean BOM
ESC BOM

A wee bit expensive tbh, but I don't really see anywhere to cut costs so whatevs, will just have to live with it.

And then just adding some actual totals as well as shipping costs:
Total

40 bucks is quite a bit for just the esc :(

## FC

After a wee while I've just finished off the first steps of the FC BOM. it is quite expensive as well :(

FC BOM

It will be cheaper when I merge it with the ESC BOM, because I'll have excess components due to MOQ but I doubt it will be a massive amount, a lot of the cost in the FC is concentrated in a few parts (the sensors pretty much) so it's a bit stink. I'll have a look on aliexpress for those parts.

---

After a few minutes of lookings its pretty obvious I'm not gonna get much cheaper on ali, the only thing which was decently cheaper was the bmp280 but it was definitely a clone chip and betaflight explicitly warns against those so I'd be very cautious going for it.

And after doing a bunch of merging, I have a final parts cost of $70.35
Merged BOM

Now just to add my other discrete components!

---

Most of the parts I'd already chosen, but for motors its a bit tricky. They're quite expensive :(

I could either source them locally for ~47 USD or buy online for ~56 USD. I'll go locally methinks

---

Argggh vrx is so expensive; i'll go with a crappy clone receiver but its still like 50 bucks :(

In other news, I think I'm done :)
The bad news is its $250 excluding shipping :(
Thats too much money nooooooo

welp i guess a bunch is coming out of my own pockets :(

For an inital start, if I exclude all the vtx stuff its only like 170 bucks which isn't terrible, so that could be an option.

---

Tallying up shipping costs, and I reckon I'll also go local for lipos, bc there are none with choice shipping and it costs like 15USD to get them here.

Kinda the same deal with the camera, but I think I'm dropping it for now anyway, so whatevs.

---

And the final totals are:
Final totals
**$217.51** - Not amazingly cheap but I'd call it doable :)

I'm gonna call it done there for today. Jobs for tomorrow:
- [ ] Update frame model to include added support struts
- [ ] Add frame to bom
- [ ] Update bom in readme
- [ ] Double check submission requirements

Overall very very very close, just the final bits where things keep popping up. Anyways, goodnight :)

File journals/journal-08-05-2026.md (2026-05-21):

# Drone Journal 25 - 08/05/2026

Man i've been so freaking busy the past few days :O
Getting back into the swing of things. After a few days I'm actually quite unhappy with the state of the shroud, so I think I'm yet again going to redesign it. This time I'm going to go for a fixed 15 degree angle, as well as shifting the camera to in front of the FC stack, to save a bit on vertical space.

New camera positioning

This will unfortunately require some rework of the frame, as I just want a couple mount points on the front, and to get rid of the rear ones.

Mounts

And after a wee bit of reejigging the battery mount (they needed to be a teensy bit wider to fit the mounts), heres the new version of the frame:
Frame pt wahtever

Hmmm, looking at this theres a very real argument for just making the mount part of the frame as opposed to a screw on part.
Camera beside frame

welp, I guess I'll just undo all of that and make that instead :)

Heres the first half of the mount:
Mount rip first bit

Obviously this wouldn't be enough to properly secure the camera so i'll also add a little ring to support the lens barrel.

And heres the finished design:
Design w/ clip

Hopefully the nylon is flexible enough to just snap the camera in but I'm not completely sure, more research could be warranted. It's also not booleaning properly in onshape but i'm genuinely so done with this part so i'll just merge it in blender later.

And heres how the drone is looking so far:
Drone

Pretty snazzy if I do say so myself :)

Only things left to add are a wee mount point for the vtx and elrs receiver, as well as figure out what I'm doing with the buzzer.

I reckon I will wrap it up here though, I'm so done with CAD :sob:

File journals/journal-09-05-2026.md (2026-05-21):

# Drone Journal 26 - 09/05/2026

Man I'm so locked in :)

Todays job is to work on the ELRS and VTX mounting.
I think I'm just gonna chuck both in the back, not too worried about wiring and stuff:
Mount

Now I need to figure out some method to actually mount these things, as they don't have any mount holes and are absolutely miniscule (10x10mm and 11x13mm respectively).

I'm torn between literally just hot glueing them in and creating a little snap fit mount, but honestly hot glue might just be easier and more secure.

Either way this is the mount style I've gone with. I had to shift them a bit left and right of each other to fit the antennae.
Mount style

Doing a tiny bit more reading and I reckon I might want to have them a wee bit further apart, supposedly they might be able to interfere with each other a bit and also it looks a bit weird lol.

I think the way to go here is just provide a couple of mounting points and then just try it when i've got the physical drone in front of me. 

Anyways, I have added a little plate at the back for both of them:
ELRS Mount cadded

What next what next ??
Hmmm ummm

heres the list again
[X] Camera Shroud
[X] Camera + VTX Mount
[ ] Finalise betaflight target
[ ] AM32 target
[ ] Submission stuff (zine, bom, renders, etc)

Wow not much. Jeepers creepers.

I guess I'll do the betaflight target lol.

---

Few minutes later and I've confirmed everything, just had to swap out one of the timer configs for the imu clkin, and make sure to enable the gyro clock generation.
Happy to call the betaflight target done :)

---

[X] Camera Shroud
[X] Camera + VTX Mount
[X] Finalise betaflight target
[ ] AM32 target
[ ] Submission stuff (zine, bom, renders, etc)

Next up, the AM32 target.

Just looked through the targets list for some similar to mine, and found that mine matches up with the B_045 configuration, so that was easy enough. Next I had to sort the voltage adc, which was just a wee bit trickier as I didn't know which adc channel it was, but after some datasheet perusing it turned out to be channel six, which is the same as most other targets. All in all, not too horrible an experience but definitely not my favourite lol.

---

[X] Camera Shroud
[X] Camera + VTX Mount
[X] Finalise betaflight target
[X] AM32 target
[ ] Submission stuff (zine, bom, renders, etc)

Ohh man this is soo close lol. I really feel like I'm forgetting something :O
I'm gonna pause for like 20 mins and eat dinner and see if I can think of anything.

---

Well I've had dinner and nothing major came up, so I reckon imma call it there for tonight. Tomorrow's mothers day, so might not be as productive but I'll try my best to get the renders, readme, and zine done, and then i'll go on a bom optimising spree :)

Tchussi!

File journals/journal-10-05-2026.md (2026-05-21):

# Drone Journal 27 - 10/05/2026

Today I'm gonna try and crank out some renders first, so pull everything into blender and do some texturing :)

---

Welp I ended up doing a little writeup on all the 3d parts and doing some exports first, but I've got everything into blender now. Actually quite a bit of work to do for the renders, and I've been fiddling around with a material for the drone chassis for a few minutes now and its hard to get good.

Drone Material

Also done a bit more looking at materials and am a bit torn between PA12 and PA12-CF.

PA12 is mjf nylon, whereas PA12-CF is fdm nylon with carbon fibre reinforcement. I'm genuinely unsure as to which would be better, PA12-CF will have more rigidity but potentially less strength due to layer lines. It would be ideal to order both imo, this also gives a backup for when I inevitibly crash lol.

---

Well I couldn't resist and I gave into the temptation of doing some simulation. I'm in the process of preparing the model for FEM in freecad, but unfortunately it is a school night, and I do have to journal before midnight, so I'll wrap it up here for today.

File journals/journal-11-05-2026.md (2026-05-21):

# Drone Journal 28 - 11/05/2026

Today is blender lock in day.

First up, a model for the ELRS receiver. This was pretty easy, just mapped a screenshot and extruded some bits.
ELRS Receiver model
Also added a roughness map, so the metal parts are a bit shiny.

Next up, the elrs antenna, just modelled it based off the pictures, and used a random plastic texture and some brass texture for the connector.
Antenna
Not super happy with the texturing yet but whatevs

Very similar process for the VTX and its antenna:
VTX
VTX Antenna

The camera model is an absolute nightmare, but I can't be bothered remaking it so this is what I'm going with:
Camera

And then I re-exported the board from KiCad as glb, which also gave me materials :)
Boards

And now its all reasonably textured.
Drone full textured

Gonna add in some cables and then call it done and start work on renders.

---

Nevermind I'm not adding cables, that is far too much of a hassle lol.

Time to do some renders, I'll just chuck it in a few environments and then do one similar to my other project with grease pencil on a transparent background.

Welp blender crashed and I hadn't saved :(
This has annoyed me and so I am quitting for now.
Goodnight

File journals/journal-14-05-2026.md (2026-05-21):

# Drone Journal 31 - 14/05/2026

Heyo yall! Today is sim day :)

Finally got some working simulations in freecad, I simplified my model even further and then also turned off second order in the mesh gen and that seemed to do the trick.

Without further ado, here are the fruits of my labor:

---

_All simulations assume 150g drone mass, 10ms collision time_
## 3m/s | 10.8 km/h 

### PA-12-HP Nylon (MJF)

10.1mm max displacement
pa12hp 3m/s 10.8km/h

### PA-12-CF Carbon Fiber Reinforced Nylon (FDM)

5.69mm max displacement
pa12cf 3m/s 10.8km/h

## 5m/s | 18km/h

### PA-12-HP Nylon (MJF)

16.83mm max displacement
pa12hp 5m/s 18km/h

### PA-12-CF Carbon Fiber Reinforced Nylon (FDM)

9.48mm max displacement
pa12cf 5m/s 18km/h

## 10m/s | 36km/h

### PA-12-HP Nylon (MJF)

33.67mm max displacement
pa12hp 10m/s 36km/h

### PA-12-CF Carbon Fiber Reinforced Nylon (FDM)

18.96mm max displacement
pa12cf 10m/s 36km/h

## 15m/s | 54km/h

### PA-12-HP Nylon (MJF)

50.5mm max displacement
PA12hp 15m/s 54km/h

### PA-12-CF Carbon Fiber Reinforced Nylon (FDM)

28.44mm max displacement
pa12cf 15m/s 54km/h

---

| Speed | PA12-HP | PA12-CF |
| ----- | --- | --- |
| 3m/s  | 10.1mm  | 5.69mm  |
| 5m/s  | 16.83mm | 9.48mm  |
| 10m/s | 33.67mm | 18.96mm |
| 15m/s | 50.5mm  | 28.44mm |

Honestly pretty decent results :)
The carbon fibre obviously looks waay better than the plain nylon, but this sim hasn't taken into account weaknesses along layer lines, which is much more of a problem in fdm prints than mjf. In terms of breaking, I would say it is possible at 10m/s and quite likely at 15m/s, which should be around the top speed of the drone.

I'd like to also quickly model another couple types of collisions, although the above one is probably most common, it'll also be pretty common to land reasonably hard on the battery. Upside down might also be a thing but it'll be tricky to model without the pcbs there

Heres a 10m/s collision:
_PA12-HP_ - 7.8mm max displacement
10m/s collision
_PA12-CF_ - 4.42mm max displacement
10m/s collision

This is a wee bit worrying, I'd really like to not bend the pcbs supports, as doing this will pretty quickly break the boards and those are expensive and hard to solder :(

I'm going to try a wee bit of cross bracing and failing that, support the force from the battery via the prop guards maybe? not super certain.

---

Same thing with straight cross bracing:

_PA12-HP_ - 6.77mm max displacement

_PA12-CF_ - 3.88mm max displacement


And with diagonal bracing
_PA12-HP_ - 6.77mm max displacement (weirdly the same lol)

_PA12-CF_ - 3.86mm max displacement


---

Hmmm well that helped but not very much. How about something else.

Added actual supportss to the frame instead of just bracing:
_PA12-HP_ - 7.66mm max displacement

_PA12-CF_ - 4.4mm max displacement

While these are worse than before by the numbers, I do think they are slightly better as there is less flex in the actual mount supports. 

And finally, straight supports:
_PA12-HP_ - 7.22mm max displacement
PA12-HP
_PA12-CF_ - 4.12mm max displacement


This is looking really good honestly, while things do move a lot, the mounts are pretty much just moving perfectly up and down, which is totally fine. A lot of the force is also going into the prop guards, which is great. I think I'll modify the design a bit to match this.

The only problem is it will make mounting the battery slightly more difficult, as it does get in the way of the rails:


I did design one more type but freecad isn't letting me mesh it and I don't have time to sort it out tonight so I'll leave it for today. Just bent the supports upwards


Annywayys
pretty productive today, this has given some good insights, and told me I almost certainly should go with carbon fiber.

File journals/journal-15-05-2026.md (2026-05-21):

# Drone Journal 32 - 15/05/2026

Holy busy day today, and tomorrow actually lol, all the drama and music stuff which so far has gone well so thats good :)

Anyways, onto the bread and butter of today, just kidding just doing some odd jobs atm.

First up I wrapped up the material sim, trying that thing I mentioned at the end of yesterday with the more curved bracing, but unfortunately ther results were pretty unimpressive, displacement is average (~7mm) which is fine, but it does bend the mounts a lot compared to just the straight supports.



---

Next up, sorting out some firmware :)
Bootloaders easy, already a prebuilt one that suits. I will however need to compile am32 for my specific target, so just going through that process now.

(I THEN PROCEEDED TO SLACK OFF AND ABANDON THE PROJECT FOR HALF A WEEK)

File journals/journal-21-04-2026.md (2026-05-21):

# Drone Journal 16 - 21/04/2026

Welp it's been a minute since my last updates on this project, but I've just wrapped up my other one so I'm getting back to work on this! 

I quickly added a debug header to the board, as well as a proper push switch for the mcu, just makes everything easier to set up and program.

---

I was also reading the docs and have eventually understood what it means by usd dfu uart connections. Basically just don't have uart devices on a couple of the ports or it can stop the mcu from booting :)

---

I've decided to add a couple more uart ports for use convenience as well, uart6, uart5, uart4, and uart2 :)
And after a bit more double checking of pin assignments and some tidying up I'm happy to call the schematic done.

Full Schematic

---

BOM
Ok I've gotten about halfway through sorting out the bom and component selection, but I'm getting pretty tired (i hate school lol) so I'm gonna head to bed early tonight.
Tchuss!

Ps - apologies for the fragmented timelapses, was working during school :)

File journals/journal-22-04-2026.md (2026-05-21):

# Drone Journal 17 - 22/04/2026 <> 23/04/2026

Did a bunch of work on the bom and it's now about done for board components :)

| Basic? | Desc | Value | Part Details | Package | JLCPCB | Num | Needed | Unit Price | Net Price | Running Total |
|---|---|---|---|---|---|-----|---|---|---|---|
| CAPACITORS | | | | | | | | | | |
| TRUE | Baro Bypass Caps (C1, C2) | 100nF | 100nF 16V X7R �10% 0402 Multilayer Ceramic Capacitors MLCC - SMD/SMT ROHS | 0402 | https://jlcpcb.com/partdetail/1877-CL05B104KO5NNNC/C1525 | 2 | 2 | $0.0013 | $0.00 | $0.00 |
| TRUE | OSD Bypass Caps (C6,C7,C8) | 100nF | 100nF 16V X7R �10% 0402 Multilayer Ceramic Capacitors MLCC - SMD/SMT ROHS | 0402 | https://jlcpcb.com/partdetail/1877-CL05B104KO5NNNC/C1525 | 3 | 3 | $0.0013 | $0.00 | $0.01 |
| FALSE | OSD Filter Electrolytic Caps (C4, C5) | 47uF | -40?~+105? 1.5mm 1000hrs@105? 10V 47uF 4mm 5mm �20% ??,D4xL5mm Aluminum Electrolytic Capacitors - Leaded ROHS | Plugin,D4xL5mm | https://jlcpcb.com/partdetail/44303-KF476M010C05RR0VH2FP0/C43312 | 2 | 0 | $0.0079 | $0.00 | $0.01 |
| TRUE | OSD Filter Caps (C9) | 100nF | 100nF 16V X7R �10% 0402 Multilayer Ceramic Capacitors MLCC - SMD/SMT ROHS | 0402 | https://jlcpcb.com/partdetail/1877-CL05B104KO5NNNC/C1525 | 1 | 1 | $0.0013 | $0.00 | $0.01 |
| TRUE | IMU Bypass Cap (C10) | 100nF | 100nF 16V X7R �10% 0402 Multilayer Ceramic Capacitors MLCC - SMD/SMT ROHS | 0402 | https://jlcpcb.com/partdetail/1877-CL05B104KO5NNNC/C1525 | 1 | 1 | $0.0013 | $0.00 | $0.01 |
| TRUE | IMU Bypass Cap (C11) | 2.2uF | 2.2uF 6.3V X5R �20% 0402 Multilayer Ceramic Capacitors MLCC - SMD/SMT ROHS | 0402 | https://jlcpcb.com/partdetail/13164-CL05A225MQ5NSNC/C12530 | 1 | 1 | $0.0028 | $0.00 | $0.01 |
| TRUE | IMU Bypass Cap (C12) | 10nF | 10nF 50V X7R �10% 0402 Multilayer Ceramic Capacitors MLCC - SMD/SMT ROHS | 0402 | https://jlcpcb.com/partdetail/15869-CL05B103KB5NNNC/C15195 | 1 | 1 | $0.0015 | $0.00 | $0.01 |
| TRUE | 3.3V LDO Bypass Caps (C13,C14) | 1uF | 1uF 25V X5R �10% 0402 Multilayer Ceramic Capacitors MLCC - SMD/SMT ROHS | 0402 | https://jlcpcb.com/partdetail/53938-CL05A105KA5NQNC/C52923 | 2 | 2 | $0.0041 | $0.01 | $0.02 |
| TRUE | IMU LDO Bypass Caps (C15,C16) | 1uF | 1uF 25V X5R �10% 0402 Multilayer Ceramic Capacitors MLCC - SMD/SMT ROHS | 0402 | https://jlcpcb.com/partdetail/53938-CL05A105KA5NQNC/C52923 | 2 | 2 | $0.0041 | $0.01 | $0.03 |
| TRUE | IMU LDO Bypass Caps (C17,C18) | 22nF | 22nF 50V X7R �10% 0402 Multilayer Ceramic Capacitors MLCC - SMD/SMT ROHS | 0402 | https://jlcpcb.com/partdetail/1884-0402B223K500NT/C1532 | 2 | 2 | $0.0019 | $0.00 | $0.03 |
| TRUE | MCU Filter Caps (C19,C20) | 100nF | 100nF 16V X7R �10% 0402 Multilayer Ceramic Capacitors MLCC - SMD/SMT ROHS | 0402 | https://jlcpcb.com/partdetail/1877-CL05B104KO5NNNC/C1525 | 1 | 1 | $0.0013 | $0.00 | $0.03 |
| TRUE | Flash Filter Cap (C21) | 100nF | 100nF 16V X7R �10% 0402 Multilayer Ceramic Capacitors MLCC - SMD/SMT ROHS | 0402 | https://jlcpcb.com/partdetail/1877-CL05B104KO5NNNC/C1525 | 1 | 1 | $0.0013 | $0.00 | $0.04 |
| FALSE | 5V Bec Output Electrolytic Cap (C22)  | 180uF | 10000hrs@105? 180uF 210m?@100kHz 3.5mm 35V 8mm 900mA@100kHz 9mm �20% ??,D8xL9mm Aluminum Electrolytic Capacitors - Leaded ROHS | Plugin,D8xL9mm | https://jlcpcb.com/partdetail/Ymin-LKMD0901V181MF/C442870 | 1 | 0 | $0.0851 | $0.00 | $0.04 |
| TRUE | 5V Bec Input Cap (C23) | 1uF | 1uF 25V X5R �10% 0402 Multilayer Ceramic Capacitors MLCC - SMD/SMT ROHS | 0402 | https://jlcpcb.com/partdetail/53938-CL05A105KA5NQNC/C52923 | 1 | 1 | $0.0041 | $0.00 | $0.04 |
| FALSE | 5V Bec Input Electrolytic Cap (C24) | 470uF | 10mm 16mm 35V 470uF 5mm 7000hrs@105? �20% ??,D10xL16mm Aluminum Electrolytic Capacitors - Leaded ROHS | Plugin,D10xL16mm | https://jlcpcb.com/partdetail/AISHI_Aihua_Group-ERS1VM471G16OT/C106703 | 1 | 0 | $0.0732 | $0.00 | $0.04 |
| FALSE | VTX Bec Output Electrolytic Cap (C27) | 180uF | 10000hrs@105? 180uF 210m?@100kHz 3.5mm 35V 8mm 900mA@100kHz 9mm �20% ??,D8xL9mm Aluminum Electrolytic Capacitors - Leaded ROHS | Plugin,D8xL9mm | https://jlcpcb.com/partdetail/Ymin-LKMD0901V181MF/C442870 | 1 | 0 | $0.0851 | $0.00 | $0.04 |
| TRUE | VTX Bec Input Cap (C26) | 1uF | 1uF 25V X5R �10% 0402 Multilayer Ceramic Capacitors MLCC - SMD/SMT ROHS | 0402 | https://jlcpcb.com/partdetail/53938-CL05A105KA5NQNC/C52923 | 1 | 1 | $0.0041 | $0.00 | $0.04 |
| FALSE | VTX Bec Input Electrolytic Cap (C25)  | 470uF | 10mm 16mm 35V 470uF 5mm 7000hrs@105? �20% ??,D10xL16mm Aluminum Electrolytic Capacitors - Leaded ROHS | Plugin,D10xL16mm | https://jlcpcb.com/partdetail/AISHI_Aihua_Group-ERS1VM471G16OT/C106703 | 1 | 0 | $0.0732 | $0.00 | $0.04 |
| TRUE | MCU Filter Caps (C28, C29) | 2.2uF | 2.2uF 6.3V X5R �20% 0402 Multilayer Ceramic Capacitors MLCC - SMD/SMT ROHS | 0402 | https://jlcpcb.com/partdetail/13164-CL05A225MQ5NSNC/C12530 | 2 | 2 | $0.0028 | $0.01 | $0.05 |
| TRUE | VTX 10V BEC CFF Cap (C31) | 4.7uF | 16V 4.7uF X5R �10% 0603 Multilayer Ceramic Capacitors MLCC - SMD/SMT ROHS | 0603 | https://jlcpcb.com/partdetail/20375-CL10A475KO8NNNC/C19666 | 1 | 1 | $0.0104 | $0.01 | $0.06 |
| DIODES | | | | | | | | | | |
| FALSE | Blue LED (D1) | | 100mW 120� 175mcd 3.1V 460nm~475nm 469nm 5mA Blue Discrete Diode Water Clear 0603 LED Indication - Discrete ROHS | 0603 | https://jlcpcb.com/partdetail/Hubei_KENTOElec-KT0603B/C2288 | 1 | 1 | $0.0101 | $0.01 | $0.07 |
| FALSE | Green LED (D2) | | -40?~+85? 10mA 130� 3.1V 517nm~527nm 66mW 780mcd Discrete Diode Green Water Clear 0603 LED Indication - Discrete ROHS | 0603 | https://jlcpcb.com/partdetail/23857064-PSC_1608U52GCG4/C22371297 | 1 | 1 | $0.0091 | $0.01 | $0.08 |
| TRUE | Schottky Diode (D3, D4) | | 1 Independent 1A 25A 40V 500uA@40V 600mV@1A SOD-323 Schottky Diodes ROHS | SOD-323 | https://jlcpcb.com/partdetail/GuangdongHottech-1N5819WS/C191023 | 2 | 2 | $0.0110 | $0.02 | $0.10 |
| TRUE | BEC Schottky Diodes (D5, D6) | | -55?~+125? 120A 40V 50uA@40V 550mV@5A 5A Independent SMA(DO-214AC) Schottky Diodes ROHS | SMA(DO-214AC) | https://jlcpcb.com/partdetail/hongjiacheng-SS54/C7420369 | 2 | 2 | $0.0442 | $0.09 | $0.19 |
| RESISTORS  | | | | | | | | | | |
| TRUE | OSD Imp. Res (R1) | 75? | -55?~+155? 50V 62.5mW 75? Thick Film Resistor �1% �100ppm/? 0402 Chip Resistor - Surface Mount ROHS | 0402 | https://jlcpcb.com/partdetail/25876-0402WGF750JTCE/C25133 | 1 | 1 | $0.0009 | $0.00 | $0.19 |
| TRUE | Cam Pulldown (R2) | 75? | -55?~+155? 50V 62.5mW 75? Thick Film Resistor �1% �100ppm/? 0402 Chip Resistor - Surface Mount ROHS | 0402 | https://jlcpcb.com/partdetail/25876-0402WGF750JTCE/C25133 | 1 | 1 | $0.0009 | $0.00 | $0.19 |
| TRUE | Volt Sense Div Res (R3) | 10k? | -55?~+155? 10k? 50V 62.5mW Thick Film Resistor �1% �100ppm/? 0402 Chip Resistor - Surface Mount ROHS | 0402 | https://jlcpcb.com/partdetail/26487-0402WGF1002TCE/C25744 | 1 | 1 | $0.0013 | $0.00 | $0.19 |
| TRUE | Volt Sense Div Res (R4) | 100k? | -55?~+155? 100k? 50V 62.5mW Thick Film Resistor �1% �100ppm/? 0402 Chip Resistor - Surface Mount ROHS | 0402 | https://jlcpcb.com/partdetail/26484-0402WGF1003TCE/C25741 | 1 | 1 | $0.0009 | $0.00 | $0.19 |
| TRUE | LED Current Lim Res (R5, R6) | 75? | -55?~+155? 50V 62.5mW 75? Thick Film Resistor �1% �100ppm/? 0402 Chip Resistor - Surface Mount ROHS | 0402 | https://jlcpcb.com/partdetail/25876-0402WGF750JTCE/C25133 | 2 | 2 | $0.0009 | $0.00 | $0.20 |
| TRUE | USB Res (R7, R8) | 22? | -55?~+155? 22? 50V 62.5mW Thick Film Resistor �1% �100ppm/? 0402 Chip Resistor - Surface Mount ROHS | 0402 | https://jlcpcb.com/partdetail/25835-0402WGF220JTCE/C25092 | 2 | 2 | $0.0011 | $0.00 | $0.20 |
| TRUE | Reverse Pol. Gate Res (R9) | 1k? | -55?~+155? 1k? 50V 62.5mW Thick Film Resistor �1% �100ppm/? 0402 Chip Resistor - Surface Mount ROHS | 0402 | https://jlcpcb.com/partdetail/12256-0402WGF1001TCE/C11702 | 1 | 1 | $0.0010 | $0.00 | $0.20 |
| TRUE | VTX BEC Div Res (R10) | 1.8k? | -55?~+155? 1.8k? 100mW 75V Thick Film Resistor �1% �100ppm/? 0603 Chip Resistor - Surface Mount ROHS | 0603 | https://jlcpcb.com/partdetail/4584-0603WAF1801T5E/C4177 | 1 | 1 | $0.0015 | $0.00 | $0.20 |
| TRUE | VTX BEC Div Res (R11) | 1.1k? | -55?~+155? 1.1k? 100mW 75V Thick Film Resistor �1% �100ppm/? 0603 Chip Resistor - Surface Mount ROHS | 0603 | https://jlcpcb.com/partdetail/23491-0603WAF1101T5E/C22764 | 1 | 1 | $0.0015 | $0.00 | $0.20 |
| TRUE | I2C Pullup Res�s (R12, R13) | 2.2k? | -55?~+155? 2.2k? 50V 62.5mW Thick Film Resistor �1% �100ppm/? 0402 Chip Resistor - Surface Mount ROHS | 0402 | https://jlcpcb.com/partdetail/26622-0402WGF2201TCE/C25879 | 2 | 2 | $0.0009 | $0.00 | $0.20 |
| TRUE | BOOT0 Pulldown Res (R14) | 10k? | -55?~+155? 10k? 50V 62.5mW Thick Film Resistor �1% �100ppm/? 0402 Chip Resistor - Surface Mount ROHS | 0402 | https://jlcpcb.com/partdetail/26487-0402WGF1002TCE/C25744 | 1 | 1 | $0.0013 | $0.00 | $0.21 |
| JACKS | | | | | | | | | | |
| FALSE | Camera Conn (J1) | 3P SH | -40?~+85? 1 1A 1mm 1x3P 3 3.05mm 3P 4.4mm 5.35mm 50V Auxiliary Solder Pin Beige Brass LCP SH Surface Mount,Vertical Tin SMD,P=1mm Wire To Board Connector ROHS | SMD,P=1mm | https://jlcpcb.com/partdetail/Megastar-ZX_SH1_03PLT/C7430452 | 1 | 1 | $0.0680 | $0.07 | $0.27 |
| FALSE | UART Conns (J2, J8, J9, J10) | 4P SH | -25?~+85? 1 1A 1mm 1x4P 3.76mm 4 4P 50V 6.3mm Beige Copper LCP SH Surface Mount,Vertical Tin SMD,P=1mm Wire To Board Connector ROHS | SMD,P=1mm | https://jlcpcb.com/partdetail/HongCheng-HCZZ00394/C7433440 | 4 | 4 | $0.0367 | $0.15 | $0.42 |
| FALSE | VTX Conn (J4) | 5P SH | -25?~+85? 1 1A 1mm 1x5P 3.76mm 4.4mm 5 50V 5P 7.3mm Auxiliary Solder Pin LCP Phosphor bronze SH Surface Mount,Vertical Tin UL94V-0 SMD,P=1mm Wire To Board Connector ROHS | SMD,P=1mm | https://jlcpcb.com/partdetail/HCTL-HC_1_05PLT/C2845373 | 1 | 1 | $0.1148 | $0.11 | $0.53 |
| TRUE | ESC Conn (J5) | 8P SH | -25?~+85? 1 10.3mm 1mm 1x8P 3.76mm 4.4mm 500mA 50V 8 8P LCP Phosphor bronze SH Surface Mount,Vertical Tin UL94V-0 SMD,P=1mm Wire To Board Connector ROHS | SMD,P=1mm | https://jlcpcb.com/partdetail/JUSHUO-AFC10_S08PCA00/C2764202 | 1 | 1 | $0.1222 | $0.12 | $0.66 |
| OTHER | | | | | | | | | | |
| FALSE | STM32F405 (U1) | | -40?~+85? 1.8V~3.6V 12bit 12bit 168MHz 192KB 1MB 32 Bit 51 ARM Cortex-M4 Built-in FLASH LQFP-64(10x10) Microcontrollers (MCU/MPU/SOC) ROHS | LQFP-64(10x10) | https://jlcpcb.com/partdetail/STMicroelectronics-STM32F405RGT6/C15742 | 1 | 1 | $4.7965 | $4.80 | $5.45 |
| FALSE | ICM-42668-P : IMU (U2) | | -40?~+85? 1.71V~3.6V 16bit 2KB 7.5uA IMU (accelerometer + gyroscope) SPI?I2C X,Y,Z X,Y,Z �16g �2000dps ????????????? LGA-14(2.5x3) Accelerometers ROHS | LGA-14(2.5x3) | https://jlcpcb.com/partdetail/TDKInvenSense-ICM_42688P/C1850418 | 1 | 1 | $11.2436 | $11.24 | $16.70 |
| | MAX-7456eui+ (U3) | Source: Aliexpress | | | https://www.aliexpress.com/item/33005990891.html | 1 | 1 | $4.47 | $4.47 | $21.17 |
| FALSE | XL1509-ADJ (VTX 3.3V BEC) (U5) | 3.3V | -40?~+125? 1 1.23V~37V 150kHz 2A 2mA 4.5V~40V Adjustable Buck Buck Built-in No SOIC-8 DC-DC Converters ROHS | SOIC-8 | https://jlcpcb.com/partdetail/2773703-XL1509ADJ/C2681227 | 1 | 1 | $0.2421 | $0.24 | $21.41 |
| FALSE | BL8072CLTR-3.3 (3.3V LDO) (U6) | 3.3V | -40?~+85?@(Ta) 1 18V 2A 3.3V 3uA 850mV@(1.5A) Fixed Positive SOT-223-3 Voltage Regulators - Linear, Low Drop Out (LDO) Regulators ROHS | SOT-223-3 | https://jlcpcb.com/partdetail/BL_Shanghai_Belling-BL8072CLTR33/C843780 | 1 | 1 | $0.1981 | $0.20 | $21.61 |
| FALSE | SGM2212-3.3XKC3G/TR (IMU LDO) (U7) | 3.3V | -40?~+125? 0.002%Vout 20V 3.3V 450mV@(800mA) 800mA 80dB@(120Hz) 80uA Fixed Short Circuit Protection?Thermal Shutdown SOT-223-3 Voltage Regulators - Linear, Low Drop Out (LDO) Regulators ROHS | SOT-223-3 | https://jlcpcb.com/partdetail/SGMICRO-SGM2212_3_3XKC3GTR/C3294699 | 1 | 1 | $0.6068 | $0.61 | $22.21 |
| TRUE | W25Q128JVSIQ TR (Flash) (U8) | | -40?~+85? 100,000 cycles 120ms@(32KB) 128Mbit 133MHz 1uA 2.7V~3.6V 20 Years 3ms SPI SOIC-8-208mil NOR FLASH ROHS | SOIC-8-208mil | https://jlcpcb.com/partdetail/WinbondElec-W25Q128JVSIQ/C97521 | 1 | 1 | $1.9100 | $1.91 | $24.12 |
| TRUE | XL1509-5.0 (5V BEC) (U9) | 5V | -40?~+85? 1 150kHz 2A 2mA 4.5V~40V 5V Buck Buck Built-in Fixed No SOIC-8 DC-DC Converters ROHS | SOIC-8 | https://jlcpcb.com/partdetail/XLSEMI-XL1509_50E1/C61063 | 1 | 1 | $0.2370 | $0.24 | $24.36 |
| FALSE | BMP280 Baro (U10) | | -40?~+85? 0.12hpa 1.5pa/K 1.71V~3.6V 1hpa 300nA 30Kpa~1.1bar I2C?SPI LGA-8(2x2.5) Pressure Sensors ROHS | LGA-8(2x2.5) | https://jlcpcb.com/partdetail/BoschSensortec-BMP280/C83291 | 1 | 1 | $6.2470 | $6.25 | $30.61 |
| FALSE | 27MHz Crystal (Y1) | 27MHz | -40?~+85? 20pF 27MHz Crystal Oscillator �10ppm �20ppm SMD3225-4P Crystals ROHS | SMD3225-4P | https://jlcpcb.com/partdetail/YXC_CrystalOscillators-X322527MSB4SI/C9008 | 1 | 1 | $0.0764 | $0.08 | $30.68 |
| FALSE | 8MHz Crystal w/ Caps (Y2) | 8MHz | -40?~+85? 10pF 40? 8MHz SMD3213-3P Ceramic Resonators ROHS | SMD3213-3P | https://jlcpcb.com/partdetail/973876-CSTNE8M00G520000R0/C907975 | 1 | 1 | $0.1909 | $0.19 | $30.88 |
| FALSE | BEC Inductors (L1, L2) | 68uH | 1.8A 2A 315m? 68uH �20% SMD,7.2x6.6mm Inductors (SMD) ROHS | SMD,7.2x6.6mm | https://jlcpcb.com/partdetail/SHOUHAN-CYA065068UH/C5189964 | 2 | 2 | $0.3052 | $0.61 | $31.49 |
| TRUE | BOOT Button (SW2) | | -30?~+80? 1.6N 100,000 cycles 12V 2mm 3mm 4mm 50mA Black Round Button SMD(SMT) Tab SPST Surface Mount,Vertical Without Bracket SMD,4x3mm Tactile Switches ROHS | SMD,4x3mm | https://jlcpcb.com/partdetail/XUNPU-TS_1088AR02016/C720477 | 1 | 1 | $0.0555 | $0.06 | $31.54 |
| FALSE | VTX Channel Select (SW1) | | 2.54mm 24V 25mA 3 Red SPST Slide, Rocked ??,P=2.54mm DIP Switches ROHS | Plugin,P=2.54mm  | https://jlcpcb.com/partdetail/100634-DSWB03LHGET/C99420 | 1 | 1 | $0.2322 | $0.23 | $31.77 |
| TRUE | Reverse Pol. Mosfet (Q1) | | 1 P-Channel 14nC@10V 30V 47m?@10V?60m?@4.5V?85m?@2.5V 4A 55pF 645pF 80pF 900mV SOT-23 MOSFETs ROHS | SOT-23 | https://jlcpcb.com/partdetail/Alpha_OmegaSemicon-AO3401A/C15127 | 1 | 1 | $0.0584 | $0.06 | $31.83 |
| FALSE | 5A Resettable Fuse | 5A | -40?~+85? 1.2A 12s 250V 2? 3.2W 5A 600mA 600m? ??,P=5.1mm Resettable Fuses ROHS | Plugin,P=5.1mm | https://jlcpcb.com/partdetail/343048-JK250600U/C369135 | 1 | 1 | $0.1795 | $0.18 | $32.01 |
| FALSE | USB Micro B Conn (J6) | | -20?~+85? 1 1.8A 30V 5,000 times 5P Black Female Micro-B Surface Mount, Right Angle USB 2.0 SMD USB Connectors ROHS | SMD | https://jlcpcb.com/partdetail/SHOUHAN-MicroXNJ/C404969 | 1 | 1 | $0.0402 | $0.04 | $32.05 |
| TOTALS | | | | | | | | | | |
| | | | | | | | | | Total: | $32.05 |

---

Its now the next day (I took a nap and then didn't wake up lol, sorry soup) and I've been doing a bit of further research into vtx stuff. My current solution is a tx5823 module, which has the downside of being extremely big. It's 22x19mm, which is pretty much the entire size of the board itself (25.5x25.5mm). This is a bit of a problem, as I'd need to basically add another layer to the stack, which wouldn't be ideal structurally.

I've been looking at other options and the rtc6705 is also possible, but this would also be quite costly, as the chip is quite hard to source (again probs just aliexpress and all the ones i'd trust are like 20 dollars). Because of this, I'm seriously considering just using an external vtx. It's pretty much what I'm doing already, the tx5823 is pretty much just a vtx module with 1 extra step (capacitors) so it's not really sacrificing any effort on the project. It would probably cost less and also have additional functionality and also be much more reliable. 

One I've got my eye on is the pandaRC nano, not the actual official one by pandarc but the aliexpress modules which it seems are just using pandaRC's name. They seem to be pretty popular and are available for like $10-$15 which is very reasonable, alongside this they're like a quarter of the size of the tx5823 which is a big bonus.

---

A wee bit of thinking later and I've decided to go with this option. This basically just means gutting the tx5823 section and just adding a vtx connector, which is basically just power, video, and uart for control. VTX's do typically require 10v however, which will require yet another bec (which will replace the vtx bec). Fortunately, because I've used an adjustable BEC it should just be a simple matter of adjusting values.

To that end, I have made the required changes and now it should just support any vtx pretty much.
BEC
CONN

A bit unfortunate but its for the greater good. Perhaps in the future I'll make my own vtx module but I think this could be good for a seperate module.

I have gone ahead and retroactively adjusted the bom, basically just excluding the vtx. I'll add it to the overall bom later, which will just be incl. the fc and esc bom + other parts (motors, frame, vtx...).

---

I've gone through and assigned all the footprints in KiCad, as well as updated the bom with a few components I had missed (just the connectors pretty much)
Bringing it into the pcb editor, and I might have a bit of a problem.
Layout

Not very ideal if I do say so myself. Main are for improvement I see is in the polarized capacitors and the inductors, but everything else is likely about as small as it'll get. So it looks like this is going to be another 2 sided pcb, not ideal but I can manage, just put all the tiny smd components on one side and I should be fine.

Anyways, I'll try and go optimise the parts a wee bit.

---

Turns out capacitors are gonna have to stay. I could do smd ones but it'll be about the same size anyway, and tht are way easier to solder.

Inductors look a biit nicer but it's still quite a lot for such a small pcb.
New inductors

I do believe that that will do me for tonight! Got to continue my physics internal tomorrow and I need to sort out a few notes so I can actually write stuff lol.

Tchuss!

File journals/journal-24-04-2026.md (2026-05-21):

# Drone Journal 18 - 24/04/2026

Going through pcb layout and it is incredibly obvious that this will not fit. Need to optimise a bit for size and the BECs are looking like prime targets.

First of all, with that vtx chip I was eyeing up, I don't actually need a 10v output, as it runs off of 5v. I do think I'll have a seperate dc-dc converter just for electrical isolation, but I definitely don't need a 2A bec, as the vtx module only uses 180mA.

---

And heres the new 5V vtx BEC
New bec

Much smaller as well which is nice.

---

Speaking of shrinking things, I can decrease the rated voltages on the 5v bec capacitors a bit, and probably optimise the inductors a lot.

Obviously the new inductor is way smaller in inductance and thus can be way smaller, down to just an 0805 chip inductor still with 2A max current.

I've also decided to just use two of the same circuit for both the BECs, theres really no disadvantages tbh

And after all of those changes this is the current state of the thing:
PCB Pre layout

My verdict: feasible???
It might fit, it'll be tight but worth a shot I reckon.
Also going with another 6 layer board; lets me get the ground planes in and because its still under 50x50mm its just 2 bucks still.

---

I've also decided to get rid of one of the uart ports, I legitimately just have no use for it and it's taking up my precious board space, so its gonna go :)

I'm also dropping the fuse, maybe a bit bad practice but there is no way it would fit.

---

Annnd boom! Everything fits :)

Layout Front
Layout Back

Time to get routing :O

---

Welp I forgot to record a looot of it but the routing is now complete (PLS REVIEWER INFLATE MY HOURS I SPENT SO LONG \[3h-ish\] YOU CAN LOOK AT THE SYSTEM CLOCK PLS PLS PLS 🙏🥺🥺🥺)

Heres the finished product :)
F Cu.
In 2 Cu.
In 3 Cu.
B Cu.

The other two internal copper layers are just ground planes (fully uninterrupted :O I'm very proud of myself lol)

USB lines are impedance matched, and I think I used adequate copper pours for the power sections.

I even fixed all the drc errors! A bunch of warnings still but they're probs all just silkscreen issues which are trivial.

Only thing I might go and do is some via fencing around the clock maybe, could be good but honestly its probably not a big deal.

Irregardless, that's gonna be me for tonight, I'm tired, want to go to bed, and need to feed soup in the next 20 mins so yeah; later alligators :)

Oooh also its a long weekend this weekend so lots of work can be done :)

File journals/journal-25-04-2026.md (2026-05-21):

# Drone Journal 19 - 25/04/2026

Hello again! Getting back into it today; doing some work on tidying up the FC pcb some more. 
It is all good to go technically, but I'd like to optimise a bit of the power stuff, just making sure all the pours and stuff are optimal, as well as checking a bit more stuff re rf signals / clocks.

---

I've added an extra ground pour to the internal signal layer (Cu 3.) because there was plenty of space for it, so hopefully that aids with heat dissipation and signal grounding stuff :)

Also connected the shield of the usb connector to ground, could have been an annoying mistake lol.

---

Next added 3d models for everything
Top
Bottom

Then fixed up the bom (bc I changed a buncha parts yesterday).

---

And after doing some exports, it's about time to call the FC done!

So I guess it's time to do what I've been procrastinating for so long and actually finish off the ESC board. Not what I want to do but I suppose its needed :(

All that I have to do is fix the drc errors, optimise some routing with the actual power carrying loops and thenmake sure I haven't forgotten anything.

---

Welp it turns out I also have to increase the via size, didn't realise it cost more so i'll rework it with the new size of vias.

Annnnd after an hour or so all the vias have been resized:
New via sizes

And now I've fixed all the drc errors ! Yippeee
No drc errors
Technically theres still like 40 or so but none of them are actually violations, its just mad that I've got pads hanging off the edge of the board and such.

I also made some tweaks to the routing, just making sure that the feedback traces were a consistent width.

---

I chucked it into jlc for a quick quote with assembly, and yeah, I don't think its happening. Twas $136 for the ESC alone :O

What I'll do is just get the board and a stencil, and order the parts from lcsc probably, and then attempt to solder it myself.

Might be quite tricky as I don't have any tools to do it, but I'm down to give it a shot lol. Worst part'll be because its two sided, so not sure how that will work but I'll figure something out.

Likely the same deal with the flight controller, but I'm completely done with doing jlc stuff for today so i'm going to pivot into the start of some CAD work.

---

Nevermind I just realised some of my parts are totally clipping together; serves me right for not adding courtyards to my footprint lol.

And now all fixed, plus I sorted out all the 3d models :)
Top 3d
Bottom 3d

---

Next up, silkscreen! I'm going to work on the FC first because the esc is annoying, so I'll report back when thats done.
FC Silkscreen Top
FC Silkscreen Bottom

Theres really just not a lot of space for any silkscreen details, especially when considering the quality level, given this is a 25x25mm board, and jlc can only print silkscreen so small. Normally I would add some art but here I'll just settle for corner fish.
corner fish

And heres the esc board; very basic because there is literally nothing to put lol.

top silkscreen
Bottom silkscreen

and another corner fish :)
corner fish v2!

And I also came up with the epic title of this project; FishPV because fish are cool 👍

---

Another quick change I've realised I should probably make is making the ESC JST connector a horizontal one rather than vertical, given the FC board is going to be stacked directly on top of it.

Nneeevermind i cant be bothered that looks like hell: future me can deal with it :)

---

Welp it turns out that I am already future me, as I've chucked everything into cad to get started on stuff and yeah, it might be a bit of a problem. I'll have a look online for low profile / right angle jst sh connectors bc that would greatly help.

No low profile ones but I think even with a smallish gap it should be fine: This is probably ok for the actual stackup, might just need slightly longer screws but overall its still very reasonable.
Its not even that much taller than it would be without the connector stuff, as the caps on the bottom of the fc hang down quite a bit as well.
Cad

Anyways, its getting a wee bit late and I don't want to start something new at this time, so I'm going to wrap it up here for the day. Tchussi!

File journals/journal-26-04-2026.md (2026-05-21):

# Drone Journal 20 - 26/04/2026

Welp guess whos back? Its me :)

CAD work today; I've decided to build my own frame instead of buying, and get it printed somewhere out of resin instead of fdm.

For CAD, i'm basing it off the betafpv air 65 II, as thats what I designed my pcbs around.

Heres my required feature set / design requirements:
- 25.5mm mounting holes
- Prop guards
- Mounts for 1102 / 1103 motors (12000-14000kV)
- 40-ish mm props
- Mount for 450-650mAh lipo, 2s
- Very crashable
- Camera mount with adjustable angle (~5-40 degrees probs)

---

I started by trying to get a motor 3d model; I found one on grabcad but the only available format was f3d and I was very quickly reminded of how much I hate autodesk. I tried (in vain) for like 20 minutes to get fusion to open on the web, before eventually kind of figuring it out (the web version was super bugged, the projects page was just on top of the editor) and managing to export as step. God i never want to touch that again.

---

Anyways, getting into it, i've decided to go with a 75mm base, so this is my initial sketch of the layout:
Start cad

And heres the base sketch for the prop guards:
Prop guards

I've opted to use M1.6 bolts for this, as thats what I designed my pcbs around and it should provide a little more strength at the cost of some weight.
For mounting the electronics stack, I want not too much support, as some springiness will help absorb impacts and not damage the electronics on a crash. Does need to be semi rigid though, otherwise the gyro and other stuff won't work perfectly.

And I think this should work ok, not entirely happy with the shape but it'll do for now :)
Board mounting

Annd now in 3d :)
3D
Its not all done but I'm very inexperienced with 3d cad (most of the things I make are just a box with a couple fillets lol). Took a while and unfortunately I have to shoot off, meeting my bestie in town for dinner :O should be fun.

Tchussi! more tmmrw

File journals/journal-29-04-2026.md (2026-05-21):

# Drone Journal 21 - 29/04/2026

Hello again! Been a couple days but yknow im back at it :O 

I've been doing more cad work, and have been doing some stuff with the board mounts, and i've got a wee bit through it, but I'm not really liking the way that its looking. Most of all, its kinda looking to be a bit springy which won't be amazing for the fc so I'm going to do a wee little redesign and try something else.
Mount braces take 1

Heres my other ideas for the mount holes:
Mount hole designs

Annd heres what I've got to finish off, I opted for the square on with a tiny bit more bracing, but again I might remove it if I feel like it later.
Cad board mount new design

And with some fillets:
filleted
Man I forgot how nice cad is, its like you just always have perfect topo :sob:

I did decide to lower the board mounts, just because my stack is a bit taller than most. Also my actual mounting holes were a bit backwards so they're better now.
Lowered mounts

And now with propeller baskets! Including motor mounts:
Prop basket w/ motor mounts

Done some material research and I've decided to go with PA12-HP Nylon, as this has really good mechanical properties. Resin is too brittle and will likely just shatter on impact, which is very bad for reusability. FDM can't get the resolution I need consistently (~2mm walls) and I can get it for only ~$4 (from jlc3dp) anyway, so it's not ridiculously expensive. With my current design, the frame would weight around 11g, which is very acceptable.

The last bit of CAD to do is just sort out the battery holder, but I'll save that for tomorrow because I am totally cadded out. Goodnight folks have a lovely day :)

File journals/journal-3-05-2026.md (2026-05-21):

# Drone Journal 23 - 03/05/2026

Welp been a few days but I'm back in action :)
Gig went well but i was utterly exhausted yesterday.

Annnnyyways, getting straight into it: Today I want to design the camera shroud for the drone, which will protect the electronics and hold the camera.

After a bit of deliberation, I've decided on this general shape: It allows a reasonable range of camera angles from 10 to 40 degrees and isn't too big.
10 degrees
40 degrees

Welp its been another 30 minutes and holy crap this is painful, I really need to learn how to properly do cad lol. However, I have decided to just call it quits and design this bit in blender. Just much easier for me in general.

And heres the inital shape:
Shape

And with some more holes chopped out of it:
Chopped

Mountings gonna be very annoying to do in blender so for that I'll chuck it back in onshape. Gonna have to wait till tomorrow though, got some IRL stuff I've got to sort.

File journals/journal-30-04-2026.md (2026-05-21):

# Drone Journal 22 - 30/04/2026

Did some more work in cad and I have designed a wee battery mount. I ended up just going for some rails which I can wrap some straps around to easily mount the battery, as opposed to going for a full like box.

Battery mount

I've also just chucked in the motors to the assembly and realised that I may have made the baskets a little too deep, as ideally the propellers would be level with the actual prop guard rings, which they won't be at the moment.

Motors

Raised up the basket a wee bit and now it's looking good :)
Better basket
Not an actual model of the propellers I'm using, as I just found some generic propeller model online and scaled it to size, but its accurate enough yknow?

And with that the main part of the frame is complete :)
Finished frame

Aaahhh I'm so close to finishing this project. Heres the list of things yet to be done:
- Camera Shroud
- Camera + VTX Mount
- Finalise betaflight target
- AM32 target
- Submission stuff (zine, bom, renders, etc)

very nearly there :)

I am going to wrap it up for today though, very big gig tomorrow and I need to do a wee bit of practice methinks.

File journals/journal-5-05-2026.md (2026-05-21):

# Drone Journal 24 - 05/05/2026

Welp I've been slacking off again :(
Goal for today is to get the camera shroud fully done. 

I've done some really screwed up editing but managed to warp the shroud to the mounting points:
Shroud

Ok this is ugly so I gave on last go at onshape and it magically works this time :)
Screw you cad i hate you :( :(

And heres the cad version of the shroud:
Cad Shroud

I am going to pull this into blender and tweak it a bit because theres some things that are being difficult, but overall much happier with the turnout.

Oopsy daisy I crashed blender :( Oh well, time to redo everything :)

Alrighty I'm about back to where I was, and if I do say so myself, everything is looking decent. This version goes for the camera mounted above the fc instead of in front of it, which should be safer on a crash? Not entirely sure but my gut says yes.
Blender

All thats left now is some connectors for the camera, and a mount for the vtx, elrs, and antennae. That will unfortunately have to be a tomorrow job, i need some sleep :O

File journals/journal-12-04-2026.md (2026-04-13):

# Drone Journal 14 - 12/04/2026

Hello again! I have been mildly slacking for the last wee while (baldurs gate is too addictive :() but I am now locked in.

More work on the flight controller today, I'm going to tackle the entire list from friday if I can, and hopefully finish off the entire schematic.

As a reminder heres the list:
- LDO for VTX (yh ik i made a typo yesterday)
- LDO for IMU
- Figure out IMU interrupt wiring
- Figure out OSD clock
- Figure out ELRS receive
- Figure out USB
- Read up on rf best practices
- Look at how to define targets for Betaflight / what pins to use for stuff

### VTX LDO

I'm going to go with another BL8072 chip for the VTX LDO, they're very easily available on JLC and LCSC, and they're super super easy to set up (no external feedback network) which is a big plus. The exact one is the BL8072CLTR33 - Just the 3.3V version of the chip.

### IMU LDO

This one has some specific reccommended requirements from the betaflight docs, so I'll have a look and see if the BL8072 meets them and if not I'll try and find a chip that does.

Unfortunately, the chip doesn't specify the noise characteristics in the datasheet, and this is rather important for the IMU, so I'm going to find another one which does.

The [MD7601A50](https://jlcpcb.com/partdetail/3391899-MD7601A50/C2978483) is looking reasonably promising; It's got a max current of 1A, and a psrr of ~80dB at 1Hz, which is well above the reccomended spec. It is worth noting that the psrr was measured with a Vout of 3.6V whereas mine would be 5V, but hopefully this doesn't cause a 10dB difference (which is like twice as loud I think?). Anyways, I'm going to go with this one.

WAIT IM STUPID THE IMU IS 3.3V AARRRGGGHHHAWDSADASDKJASDJLA

Actually the [SGM2212](https://jlcpcb.com/partdetail/SGMICRO-SGM2212_3_3XKC3GTR/C3294699) looks good, its got about the same specs but 3.3V :)

LDO's

### IMU Interrupt Wiring

I finally got around to looking in the hardware development channel on the discord and my goodness there is a lot of good material :) I someewhat quickly figured out what to do with the IMU interrupts. One pin (INT2) is actually the clock input for the IMU, which I've connected to TIM10, a random generic timer on the MCU. It should work but I'll have a look round for any other target files doing the same thing, pretty easy to move it later if necessary. The other pin is just an interrupt which goes to any gpio on the MCU, defined in the target file. For now I'm just copying the target file for the [Acci FPV](https://www.pcbway.com/project/shareproject/Acci_FPV_Flight_Controller_Betaflight_STM32F405_AT32F435_48fb0ecb.html) FC, bc its pretty overwhelming to just start chucking stuff in with no rhyme or reason lol.

_I'm considering moving the time to TIM1_CH1N if its compatible, because it is physically next to the IMU int pin, but I could just as easily move the IMU int pin._

### OSD Clock

Did some more hunting around and found that I probably should be using an external clock for the OSD chip; Also it seems that HSYNC and VSYNC aren't actually required, and the chip can determine it from VIN (I keep on confusing this for voltage lol, its video).

The required clock is 27MHz which should be easy enough, just some additional considerations with placement but I do tend to find them reasonably forgiving (albeit I've only used them in low frequency applications, with the rf stuff nearby it might be a bit more important, although that is 5.8GHz compared to 27MHz, could be less interplay?)

_Note to self, I need a crystal, not a crystal oscillator :O_

OSD Schematic

### ELRS 
ELRS just connects over UART and is typically set up as a generic UART port on the flight controller which the user can plug any uart peripheral into and then configure in betaflight. This poses an interesting consideration which is whether I want these generic peripheral ports, as this is a tinywhoop controller and my board space is very limited, I have a feeling its going to be a matter of if I've got space then sure.

For now I'll continue as if I'm only having ports for predetermined peripherals.

Anyways, I've connected the ELRS port to UART1.

### Blackbox

Extra features! OMG :O
Really though, I do need some blackbox storage on board as it's super necessary for tuning and a variety of other things. I'll just use a generic flash memory chip, and the best choice seems to be a [W25Q128JVSIQ](https://jlcpcb.com/partdetail/WinbondElec-W25Q128JVSIQ/C97521) chip, which is a basic part in jlc and has 128Mbit memory, which should be plenty.

Blackbox Schematic

### LEDs

Betaflight likes you to have a few LEDs for status stuff, so i'll have two, one blue, one red.
They just get wired to a couple GPIO pins, super easy :)
LEDs

### Beeper (Buzzer?)

Whatever it's called its also super easy to wire up, literally just plug it into a gpio again.
Buzzer

### Other stuff I did
I did a bunch of other generic stuff, wiring up a bunch of spi ports for the gyro, flash, and osd. Also added the ESC connector which I realized I had completely forgotten lol. I also added ADC for current sense and voltage sense. I might just do voltage sense on the FC board, which should also free up a bit of space on the ESC board again. I didn't realize it was typical to just do it on the FC at the time which is why I added it, but it only being on one motor mcu is probably going to cause problems later anyway so I'll cut it out.

I also did a bunch of cleanup on the schematic and it's looking much prettier now:
Full schematic so far

Thats going to be me for this project today, gonna go and do some work on my audio thingy which should be fun. See ya later alligators!

---

Side notes for today!

- VTX I could use the [RTC6705](https://datasheet4u.com/pdf-down/R/T/C/RTC6705-RichWave.pdf) instead, it seems much more common and is mentioned explicitly in the betaflight documentation so probably a pretty decent idea.
- Pinout of stm32 [here](https://betaflight.com/assets/files/stm32f405_pins_timers_dma-e7ae8fce49c50af781149b0458e4ac87.pdf), use the lqfp64 column bc thats the package im using on jlc
- Don't need rssi adc - old fashioned and elrs has it over uart

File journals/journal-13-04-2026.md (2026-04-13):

# Drone Journal 15 - 13/04/2026

Back to work I am!
Goals for today are pretty much to finish off the schematic, which off the top of my head involves:

- Checking out that other vtx chip
- Double checking clock circuit (might need external caps?)
- Additional uart ports
- Writing up a betaflight target (will help make sure I didn't miss anything lol)
- USB connection
- Proper power chain protection

### VTX Chip

Well it turns out this chip isn't really easily available anywhere (it's like thirty bucks on aliexpress :O) and also the open source implementation of it looks mightily scary lol.

I'll stick with my current approach and it should hopefully work; Even if mildly iffy.

---

Well it turns out it's kinda the same deal with the chip i'm using at the moment :(. 30NZD from aliexpress and not available from jlc or lcsc so I'll do a bit more research on other options.

---

Nothing obvious has come up; A lot of stuff is just bluetooth / wifi transceivers, so it makes it quite difficult to find the chips I'm looking for. Atp, I'm considering just using an external vtx, as they're only an extra like 15NZD, and are guaranteed to work much better than what I build.

I'll do more thinking on this later.

### Clock Circuit

Ok the datasheet says I don't need external capacitors, but that my crystal does have to be a _parallel resonant, fundamental mode
crystal_. No idea what that means but I'm sure I can find that when it comes to selecting the actual components.

### USB Connection

Usb is pretty easy again, just going with micro b because I have a bunch of them + they're super easy.

### Power chain protection

I found a super handy guide on the discord:
Power guide

And here is my modified version for the setup I'm using:
My power setup
The reason for the 4.5V is because of the diodes voltage drop. 

Pretty easy setup in the schematic, just a tiny bit of swapping out symbols (kicad doesn't have a 4.5v power symbol grrrr).

Power section

Another little thing I want is reverse polarity protection for the battery. The other design I'm using as reference also had a fuse, which would be a mightily worthy addition.
The zener diode from the reference is mostly unnecessary for me, as my Vgs will never get above ~8V due to me using 2s batteries.

Reverse Polarity Protection

The final thing to do with the power section (pretty much) is to swap out the 5v ldo with a dc-dc buck converter. All peripherals run off 5v and it uses a lot of current and LDO's generate a lot of heat. Buck converters are just way more efficient and thus are reccomended for this. I might also have another one seperate for the vtx as with rf stuff it could cause a bunch of noise on things that don't want it.

Heres the bit for the main 5V line:
5V BEC

And the vtx BEC:
3.3V BEC

### Betaflight target

Pretty self explanatory, I've done all of what I understand atm, (no timer setup just yet) but theres still a bit left to do. 

### Adding barometer

I've also decided that I'd like to inclued a barometer in this drone, because that enables me to have a hold altitude mode which would be greatly appreciated I think (good for tuning as well).
Pretty easy to set up, I'd already used the i2c1 pins though so I chucked it on i2c2.

### MCU crystal

I found an 8MHz crystal with built in caps on jlc, so I chucked that in. Betaflight reccommends 8MHz for my IMU and mcu combo.

I'm going to take a quick break and figure out what else I need to do today, if I don't get anything then I'll just move onto my other project for now. See ya later (maybe?)

Progress for now:
FC Schematic progress

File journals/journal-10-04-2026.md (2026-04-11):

# Drone Journal 13 - 10/04/2026

Hello again!
It's been a few days because of various irl events etc... but I am getting back into it!
Today I've decided to do a bit of work on the flight controller board. The ESC still needs a bit of effort put into it but its going to be quite tedious and boring so I'm leaving that for another day, for now, I'll get to work. First step is to find some kind of typical application schematic for my MCU, which is the STM32F405.

---

I've started placing some stuff down on the board and just making sure I've got everything I need. I've also been looking at a few open source flight controllers to steal some ideas from them and its been quite helpful. I've decided to add a buzzer, and remembered I need USB.

---

Starting to figure out voltage regulator:
- MCU says ~100mA from datasheet
- IMU will probs be <30mA (datasheet says 3-6 but i'm not sure if I read the right parameter lol)
- Camera doesn't say but I'll say ~150mA as a guess
- OSD says max ~150mA 
- ELRS receiver will probs be ~100mA
- Buzzer will be ~50-100mA
- TX5823 is max ~350mA

This gives a total of ~1A, and just to be safe I'll go for 2A.
I quickly foundan LDO which seems decent for the task:
[BL BL8072CLTR50](https://www.lcsc.com/product-detail/C692268.html)
It's got a dropout voltage of ~1.0V at 5V output at 2.0A, which just means my battery voltage can't go below 6V, which is perfect, as this is the voltage of a fully discharged 2S battery. It does mean that I won't be able to use 1S batteries, but I think that was probably already the case from the ESC, except I didn't check lol.

I spent quite a while trying to figure out what resistors I needed before realizing the chip was a fixed output voltage one lol. Anyways, I'm going to start connecting stuff up and report back soon!

---

Sorting out the vtx now, and the chip I'm using just has a dip switch method for channel selection. Most VTX's connect to betaflight and allow configuration through that, but for the sake of simplicity, I'm going to go with a manually configured one, completely bypassing any betaflight things and just taking direct camera signal and transmitting it.

The chip has 3 bit channel selection, so 8 channels total, which are listed in the [datasheet](https://www.scribd.com/document/720542539/TX5823-Spec-V1).

It doesn't have any output power seleciton, but just chucking a resistor before the antenna should work fine, maybe with a switch to select output power and stuff.

---

I'm going to leave out a microphone for now but it could be a nice addition if I've got extra space on the board.

---

Annndd I just realized the vtx IC is 3.3v :( need yet another voltage regulator

---

MAX7456 (OSD IC) has an internal clock but also supports external clock, not sure if I should leave the clock pins floating or ground them.

---

Gyro has to use SPI because I'm using betaflight.
Hardware guide also says you must use a seperate ldo and circuit for the IMU, so I guess I'll have another lol.

---

Welp I'm going to finish up for the day. There a bunch more to do still, so heres my list for tomorrow:
- LDO for OSD
- LDO for IMU
- Figure out IMU interrupt wiring
- Figure out OSD clock
- Read up on rf best practices
- Look at how to define targets for Betaflight / what pins to use for stuff
- Figure out ELRS receive
- Figure out USB

Heres the schematic insofar, its quite unorganized but thats yet again a job for later :)
Schematic so far

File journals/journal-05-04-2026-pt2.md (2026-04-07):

# Drone Journal 11 - 05/04/2026

Welp I have received clarification from Tirthak that it is ok (ty tirthak :))
I'll layout and route with this and hopefully it all goes well.

---

I have decided I'll go back to single mosfets, the smaller size makes layout a lot easier even if there are more of them.

---

A wee bit through the layout now; Things are going well! I've just decided to have only one LED, instead of four. They were all just from the same power source anyway so not much point in having multiple, as it gives no additional information.

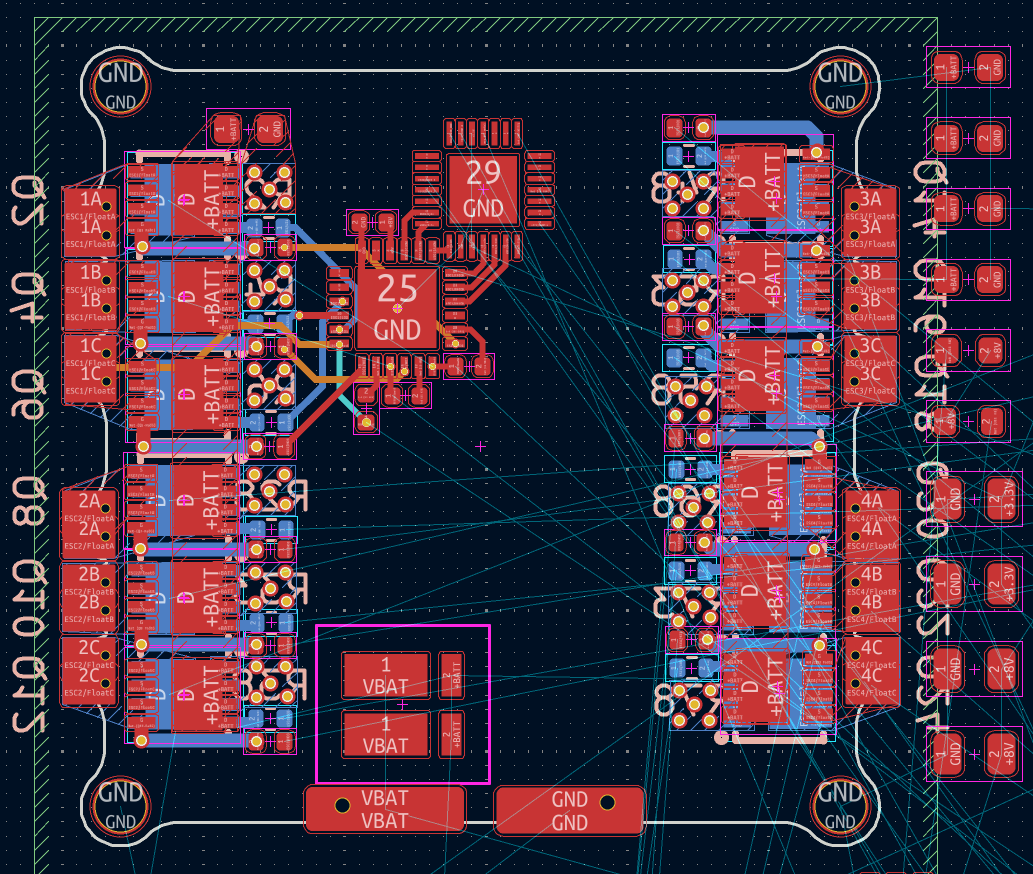
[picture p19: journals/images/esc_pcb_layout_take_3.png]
PCB so far


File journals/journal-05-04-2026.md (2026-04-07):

# Drone Journal 10 - 05/04/2026

I've started routing the board out, but it is incredibly difficult. I'm going to keep trying for another few minutes, but I think I might need to change something.

---

Yeah I'm definitely changing something, this layout is practically impossible to work with \:(

I've got a couple of ideas to save a bit of space, so I'll try those. First idea is to use resistor arrays where possible (probably just the bemf dividers). Second is to just have less decoupling. I think I could probably just have one shared group of bulk decoupling, and then keep the local decoupling (100nF) as well.

---

I've gone ahead and done the afforementioned changes, and I think it's probably not a bad idea to redo the board layout. I've learnt a bit since the last time so I reckon it'll help in the long run.

---

Ok well I got a bit into the layout, but I was again going to need to try a different approach. Unfortunately, KiCad crashed (again) and I yet again lost my progress. I'm getting a bit fed up with it, and I know it's bc I'm on wayland, so I'm going to just use windows for now \:(

---

Hello from windows!

I've been looking at some other dual channel mosfets (basically two mosfets in one package) and I've found two possible contenders: 

| Chip | Id | Vds | Rds (on) @10V | Package Size |
|---|---|-----|---|---|
| VISHAY SI4204DY  | 18-20A | 20V | 4.6mOhm | SO-8 (4x5mm) |
| VISHAY SQJB46ELP | 30A | 40V | 8mOhm | SO-8L Dual (5x5mm) |

They should both be adequate but I think I'll go with the SQJB46ELP; It's got more headroom for virtually the same package size, and cooling is better given its a POWERPAK package. The gate capacitance is also around the same, so it's even more an easy choice to make.

---

Getting a bit into the new layout and it's clear this is also not going to work. However... I have just read that JLCPCB offers free via in pad for 6 layer boards under 50x50mm, which is still just $2...

This is an absolute game changer for this project, and should make it near effortless to route the board. I think I will go this route, and use the SQJB46ELP mosfets as they're better suited anyway.

Before I do this though, I will double check in the slack.

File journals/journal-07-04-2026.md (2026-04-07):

# Drone Journal 12 - 07/04/2026

Hello again! I had a break day yesterday but I am getting straight back into it!
More pcb layout today, so I'll check in once thats progressing.

---

Progress Report 1 

I've slightly changed the footprint of the board, adding little offsets for the battery connectors and the jst sh connector.
I am also considering swapping out the bemf resistor arrays back to regular resistors, but I'll try a different distribution of stuff and see how that goes.

---

Progress Report 2

I've finished off the layout + routing of ESC1, and I was struggling with the second, but I've just layed out all the big chips on the board and realised that I've actually got a crapton of space lol. I'll be a bit more lenient with routing and placement now which should make everything a wee bit easier.

...Nevermind I forgot I still had to put all the power stuff :(

---

OH MY GOD IT"S FINALLY DONE!

LOOK AT THIS:
Front
Back
Inner layers:
Inner 1
Inner 2
Inner 3
Inner 4

I am immediately logging off for the day. Theres undoubtedly more work to do (I don't even want to look at the DRC) and I probably need to optimise the high power paths a bit more, but thats a job for another day.

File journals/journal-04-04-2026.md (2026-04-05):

# Drone Journal 9 - 04/04/2026

Welcome back folks! Today is layout time \:O
I'll just get straight into it and report back occasionally through the process!

---
First report!
I'm going to quickly redo the maths on this shunt resistor, it looks really small and I'm not sure if 3w is enough lol.

> P = I<sup>2</sup> x R
> P = 60<sup>2</sup> x 0.5*10<sup>-3</sup>
> P = 1.8 W

I'd like to give a bit more headroom than `3W` I think, so I might look at getting a `5W` one.

Alright I found one pretty easily, and its only very slightly bigger than my current one and has a `5W` rating \:)

---

Second report!

I've layed out most of the stuff but yet again I'm not going to have enough space. I think if I can swap the 0603 10k resistors with an 0402 version it will greatly help. The only reason they're 0603 in the first place is because the only option for the part on jlcpcb requires a min order of 9000 parts. What I might do is bite the bullet and use non basic parts for those resistors, which will just mean an extra 2 dollars.

---

Third report!
I've also decided to shrink the gate resistors slightly, down from 0603 to 0402 (100mW to 62.5mW). This should be fine as they don't see a lot of continuous current (only high current pulses to charge the mosfet when switching). This should be something to consider when stuff does break though, as it's not quite as good as 100mW resistors.

---

BREAK TIME i have a band practice!

---

Break done back to work!

---

Fourth report!

Ferrite beads are going! They're big and probably unnecessary.

---

Fifth report!
Just realised my voltage sensing is copied across all 4 MCU's, only need one so I'll just chuck it on the bit with the most space, which looks to be ESC 3.

---

Layout is done!
I'm not sure if its physically possible to route this, but I'll just adjust the layout as I go as necessary. Hopefully its relatively painless lol.

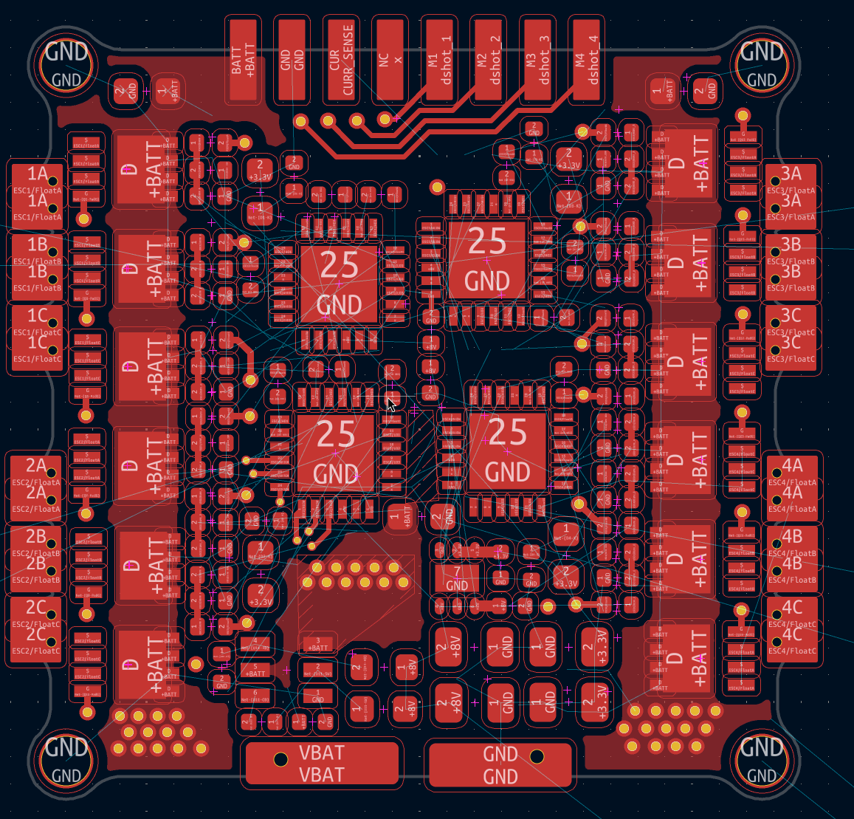
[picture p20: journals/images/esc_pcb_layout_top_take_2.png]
Board layout top

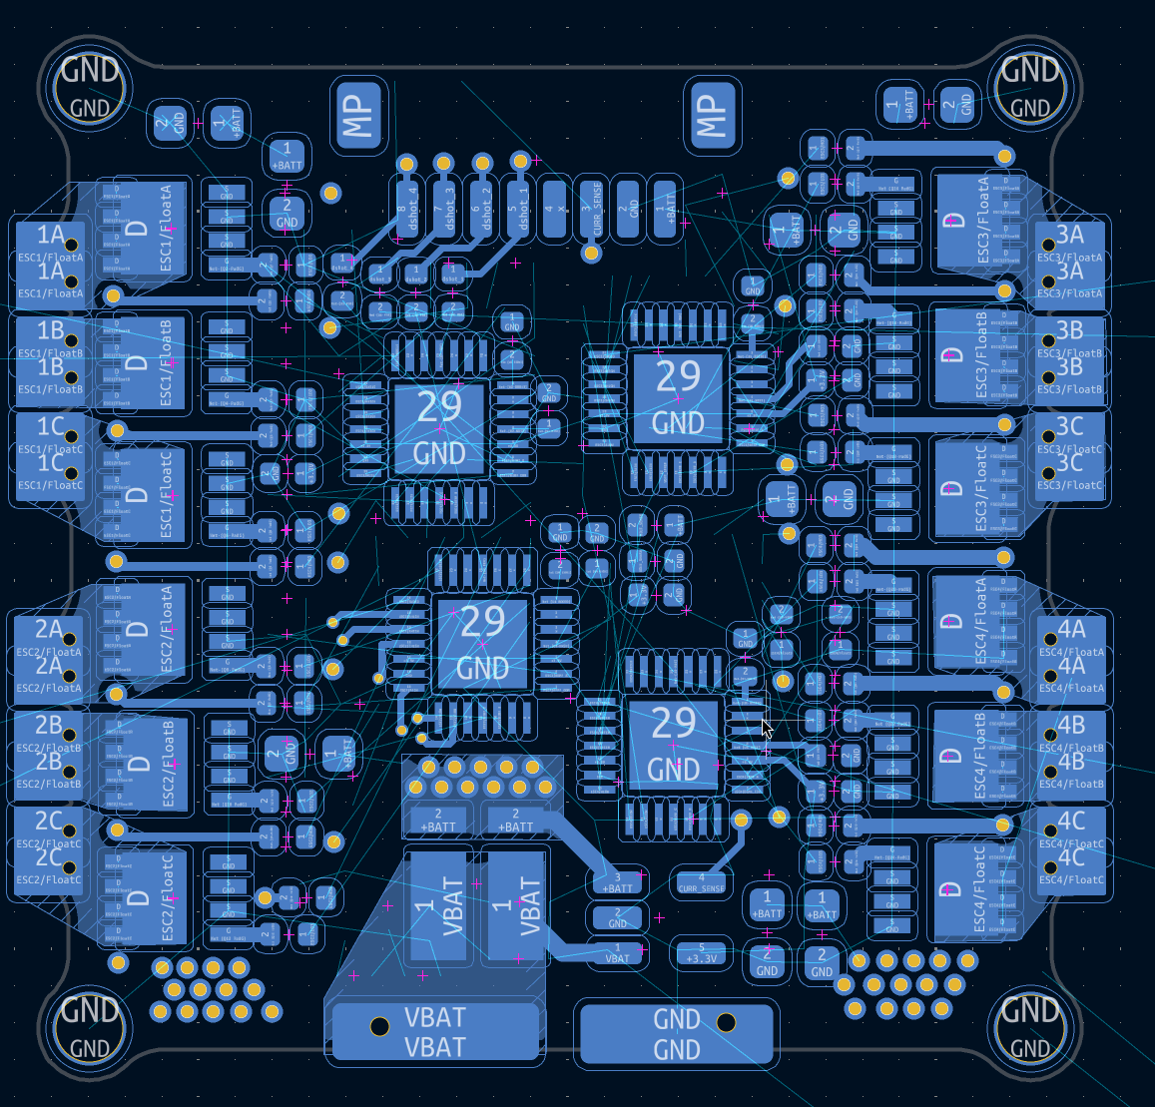
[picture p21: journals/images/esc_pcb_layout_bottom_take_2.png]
Board layout bottom


I'm going to once again split the journal here, I might do a bit more work but I want to play satisfactory before my crunch day tomorrow where I'll do a bunch of work.

Thats all for tonight! Much love :3

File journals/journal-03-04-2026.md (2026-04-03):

# Drone Journal 8 - 03/04/2026

Today I'm going to spec some components (again), relayout the board for the new format, and then if I have time, layout the components and maybe even route the board!

While I'm going through, I'm going to note a couple tradeoffs and decisions I've made, so if something breaks, I know whats likely to blame:

---

- Bemf Resistors - Gone with 100mW, should be fine but I haven't done the maths. Just from looking at it I'd say theres little to no current flowing.
- Bootstrap Caps - 0402 might be too small, but everything else is fine.
- VDD Bypass caps - I changed from 4x22uF to 3x10uF, which is still well above the 1uF needed for the bootstrap caps. 25V should be good because battery is max ~8v.
- 10k volt sense div resistor - Could have done 0402, but jlc parts required a min order of 9000, just went to 0603.
- Need to redo maths of shunt resistor for new target current.

---

Side project, redoing shunt resistor maths!

did it and `0.5mR` shunt resistor seems good, gives 132A max current which is reasonable, and power heat is manageable (~1.5W).

---

Alrighty, the bom is redone!
|Basic?|Desc |Value |Part Details |Package |JLCPCB |Num|Unit Price|Net Price|Running Total|
|---|---|---|---|---|---|---|---|---|---|
|TRUE  |Mosfet Gate Resistors (R1-R6, ...) |20r |-55℃~+155℃ 100mW 20Ω 75V Thick Film Resistor ±1% ±100ppm/℃ 0603 Chip Resistor - Surface Mount ROHS |0603 |https://jlcpcb.com/partdetail/23677-0603WAF200JT5E/C22950 |24 |$0.0016 |$0.04 |$0.04 |
|TRUE  |BEMF Div Resistor (R9, R12, R15, ...) |10k |-55℃~+155℃ 100mW 10kΩ 75V Thick Film Resistor ±1% ±100ppm/℃ 0603 Chip Resistor - Surface Mount ROHS |0603 |https://jlcpcb.com/partdetail/26547-0603WAF1002T5E/C25804 |12 |$0.0013 |$0.02 |$0.05 |
|TRUE  |BEMF Div Resistor (R11, R13, R16, ...) |1k |-55℃~+155℃ 1kΩ 50V 62.5mW Thick Film Resistor ±1% ±100ppm/℃ 0402 Chip Resistor - Surface Mount ROHS |0402 |https://jlcpcb.com/partdetail/12256-0402WGF1001TCE/C11702 |12 |$0.0007 |$0.01 |$0.06 |
|TRUE  |BEMF Div Resistor (R10, R14, R17, ...) |10k |-55℃~+155℃ 100mW 10kΩ 75V Thick Film Resistor ±1% ±100ppm/℃ 0603 Chip Resistor - Surface Mount ROHS |0603 |https://jlcpcb.com/partdetail/26547-0603WAF1002T5E/C25804 |12 |$0.0013 |$0.02 |$0.08 |
|TRUE  |Bootstrap Cap (C1-C3, ...) |100nF |100nF 50V X7R ±10% 0402 Multilayer Ceramic Capacitors MLCC - SMD/SMT ROHS |0402 |https://jlcpcb.com/partdetail/291005-CL05B104KB54PNC/C307331 |12 |$0.0043 |$0.05 |$0.13 |
|TRUE  |VDD Bypass Caps (C8-C10, ...) |10uF |10uF 25V X5R ±20% 0603 Multilayer Ceramic Capacitors MLCC - SMD/SMT ROHS |0603 |https://jlcpcb.com/partdetail/97651-CL10A106MA8NRNC/C96446 |12 |$0.0180 |$0.22 |$0.35 |
|TRUE  |Volt Sense Div Resistor (R18, ...) |10k |-55℃~+155℃ 100mW 10kΩ 75V Thick Film Resistor ±1% ±100ppm/℃ 0603 Chip Resistor - Surface Mount ROHS |0603 |https://jlcpcb.com/partdetail/26547-0603WAF1002T5E/C25804 |4  |$0.0013 |$0.01 |$0.35 |
|TRUE  |Volt Sense Div Resistor (R19, ...) |100k |-55℃~+155℃ 100kΩ 50V 62.5mW Thick Film Resistor ±1% ±100ppm/℃ 0402 Chip Resistor - Surface Mount ROHS |0402 |https://jlcpcb.com/partdetail/26484-0402WGF1003TCE/C25741 |4  |$0.0008 |$0.00 |$0.35 |
|TRUE  |ESC Indicator LED (D1, ...) |NA |-40℃~+85℃ 1.8V~2.4V 120° 20mA 300mcd 40mW 615nm~630nm 645nm Discrete Diode Red Water Clear 0603 LED Indication - Discrete ROHS |0603 |https://jlcpcb.com/partdetail/Hubei_KENTOElec-KT0603R/C2286 |4  |$0.0065 |$0.03 |$0.38 |
|TRUE  |ESC Indicator LED Resistor (R20, ...) |2.2k |-55℃~+155℃ 2.2kΩ 50V 62.5mW Thick Film Resistor ±1% ±100ppm/℃ 0402 Chip Resistor - Surface Mount ROHS |0402 |https://jlcpcb.com/partdetail/26622-0402WGF2201TCE/C25879 |4  |$0.0008 |$0.00 |$0.38 |
|TRUE  |ESC Decoupling Capacitors (C4, C6, ...) |100nF |100nF 50V X7R ±10% 0402 Multilayer Ceramic Capacitors MLCC - SMD/SMT ROHS |0402 |https://jlcpcb.com/partdetail/291005-CL05B104KB54PNC/C307331 |8  |$0.0043 |$0.03 |$0.42 |
|FALSE |Mosfets (Q1-Q6, ...) |NA |-55℃~+150℃ 1 N-channel 1.5V 1.675nF 2.9mΩ@10V、4.2mΩ@4.5V 26nC@20V 31pF 395pF 40V 55W 75A N-Channel PDFN-8L(3x3) MOSFETs ROHS |PDFN-8L(3x3) |https://jlcpcb.com/partdetail/Siliup-SP40N03GNJ/C22466709 |24 |$0.2194 |$5.27 |$5.68 |
|TRUE  |Dshot Resistor (R8, ...) |1k |-55℃~+155℃ 1kΩ 50V 62.5mW Thick Film Resistor ±1% ±100ppm/℃ 0402 Chip Resistor - Surface Mount ROHS |0402 |https://jlcpcb.com/partdetail/12256-0402WGF1001TCE/C11702 |4  |$0.0007 |$0.00 |$5.69 |
|TRUE  |Boot0 Resistor (R7, ...) |10k |-55℃~+155℃ 100mW 10kΩ 75V Thick Film Resistor ±1% ±100ppm/℃ 0603 Chip Resistor - Surface Mount ROHS |0603 |https://jlcpcb.com/partdetail/26547-0603WAF1002T5E/C25804 |4  |$0.0013 |$0.01 |$5.69 |
|TRUE  |NRST Capacitor (C5, ...) |100nF |100nF 16V X7R ±10% 0402 Multilayer Ceramic Capacitors MLCC - SMD/SMT ROHS |0402 |https://jlcpcb.com/partdetail/1877-CL05B104KO5NNNC/C1525 |4  |$0.0013 |$0.01 |$5.70 |
|TRUE  |Ferrite Bead (FB1, ...) |100R-100MHz|1 100Ω@100MHz 150mΩ 800mA ±25% 0805 Ferrite Beads ROHS |0805 |https://jlcpcb.com/partdetail/Sunlord-GZ2012D101TF/C1015 |4  |$0.0149 |$0.06 |$5.76 |
|FALSE |ESC MCU (U2, ...) |NA |-40℃~+105℃ 120MHz 16KB 2.4V~3.6V 23 32 Bit 64KB ARM Cortex-M4 Built-in+External FLASH QFN-28-EP(4x4) Microcontrollers (MCU/MPU/SOC) ROHS |QFN-28-EP(4x4) |https://jlcpcb.com/partdetail/ARTERY-AT32F421G8U7/C2765098 |4  |$0.8444 |$3.38 |$9.13 |
|FALSE |ESC Mosfet Gate Driver (U1, ...) |NA |-40℃~+125℃ 1.2A 1.5A 15ns 40ns 5V~20V 700uA IGBT、MOSFET Three Phase Under Voltage Protection QFN-24-EP(4x4) Gate Drivers ROHS |QFN-24-EP(4x4) |https://jlcpcb.com/partdetail/WXNSIC-NSG2065Q/C41414478 |4  |$0.4667 |$1.87 |$11.00 |
| |MAIN BOARD COMPONENTS NOW | | | | | | |$0.00 |$11.00 |
| |Current Sense Amplifier (U3) |NA |-26V~+26V -40℃~+125℃ 0.05uA 1 100dB 100nA 197uA 1uV/℃ 2.7V~5.5V 200mV~26V 210kHz 25uV 2V/us 40nV/√Hz@1kHz 5.5V 50V/V 8mA SOT-23-5 Current Sense Amplifiers ROHS |SOT-23-5 |https://jlcpcb.com/partdetail/TexasInstruments-INA180B2IDBVR/C2861539 |1  |$0.4206 |$0.42 |$11.42 |
|FALSE |8V Regulator (U11) |NA |-40℃~+150℃@(TJ) 1 1.1MHz 2A 4.5V~36V 40uA 600mV~34.2V Adjustable Buck Buck Built-in Yes SOT-23-6 DC-DC Converters ROHS |SOT-23-6 |https://jlcpcb.com/partdetail/TexasInstruments-LMR51420YFDDCR/C7296200|1  |$1.1808 |$1.18 |$12.60 |
|FALSE |3.3V Regulator (U10) |NA |-40℃~+125℃@(Tj) 1 1.4V@(1A) 16V 1A 3.3V 46dB@(1MHz) 50uA 60uVrms Fixed Over Current Protection、Over Temperature Protection、Soft Start Positive WSON-6(2x2) Voltage Regulators - Linear, Low Drop Out (LDO) Regulators ROHS|WSON-6(2x2) |https://jlcpcb.com/partdetail/TexasInstruments-TLV76733DRVR/C2848334  |1  |$0.2151 |$0.22 |$12.82 |
|FALSE |Shunt Resistor (R21) |0.5mr |0.5mΩ 3W Current Sense Resistor SMD ±1% ±50ppm/℃ 1206 Current Sense Resistors / Shunt Resistors ROHS |1206 |https://jlcpcb.com/partdetail/Milliohm-HoSRX1206_3W_0_5mR_1/C18724161 |1  |$0.3060 |$0.31 |$13.12 |
|FALSE |Inductor (L1) |470nH |3.8A 38mΩ 470nH 4A ±20% 0603 Power Inductors ROHS |0603 |https://jlcpcb.com/partdetail/XR-XRIM160808SR47MBCD/C48391583 |1  |$0.1348 |$0.13 |$13.26 |
|TRUE  |Main Board Decoupling Capacitors (C57, C58, C61, C62)|100nF |100nF 50V X7R ±10% 0402 Multilayer Ceramic Capacitors MLCC - SMD/SMT ROHS |0402 |https://jlcpcb.com/partdetail/291005-CL05B104KB54PNC/C307331 |4  |$0.0043 |$0.02 |$13.27 |
|TRUE  |Main Board Filtering Capacitors (C59, C60, C63, C64) |22uF |22uF 25V X5R ±20% 0805 Multilayer Ceramic Capacitors MLCC - SMD/SMT ROHS |0805 |https://jlcpcb.com/partdetail/46786-CL21A226MAQNNNE/C45783 |4  |$0.0316 |$0.13 |$13.40 |
|TRUE  |Main Board Voltage Div Resistor (R83) |10k |-55℃~+155℃ 100mW 10kΩ 75V Thick Film Resistor ±1% ±100ppm/℃ 0603 Chip Resistor - Surface Mount ROHS |0603 |https://jlcpcb.com/partdetail/26547-0603WAF1002T5E/C25804 |1  |$0.0013 |$0.00 |$13.40 |
|FALSE |Main Board Voltage Div Resistor (R82) |124k |-55℃~+155℃ 100mW 124kΩ 75V Thick Film Resistor ±1% ±100ppm/℃ 0603 Chip Resistor - Surface Mount ROHS |0603 |https://jlcpcb.com/partdetail/23515-0603WAF1243T5E/C22788 |1  |$0.0014 |$0.00 |$13.40 |
|FALSE |JST Connector (J1) |NA |-25℃~+85℃ 1 10mm 1A 1mm 1x8P 2.9mm 4.32mm 50V 8 8P Auxiliary Solder Pin Copper alloy PA SH Surface Mount, Right Angle Tin UL94V-0 White SMD,P=1mm,卧贴 Wire To Board Connector ROHS |SMD,P=1mm,Surface Mount，Right Angle|https://jlcpcb.com/partdetail/JST-SM08B_SRSS_TB_LF_SN/C160407 |1  |$0.3062 |$0.31 |$13.71 |

Looks simply splendid!

Now it's time to reassign all my footprints \:)
...
Done! Board now looks like this, much more manageable I reckon.

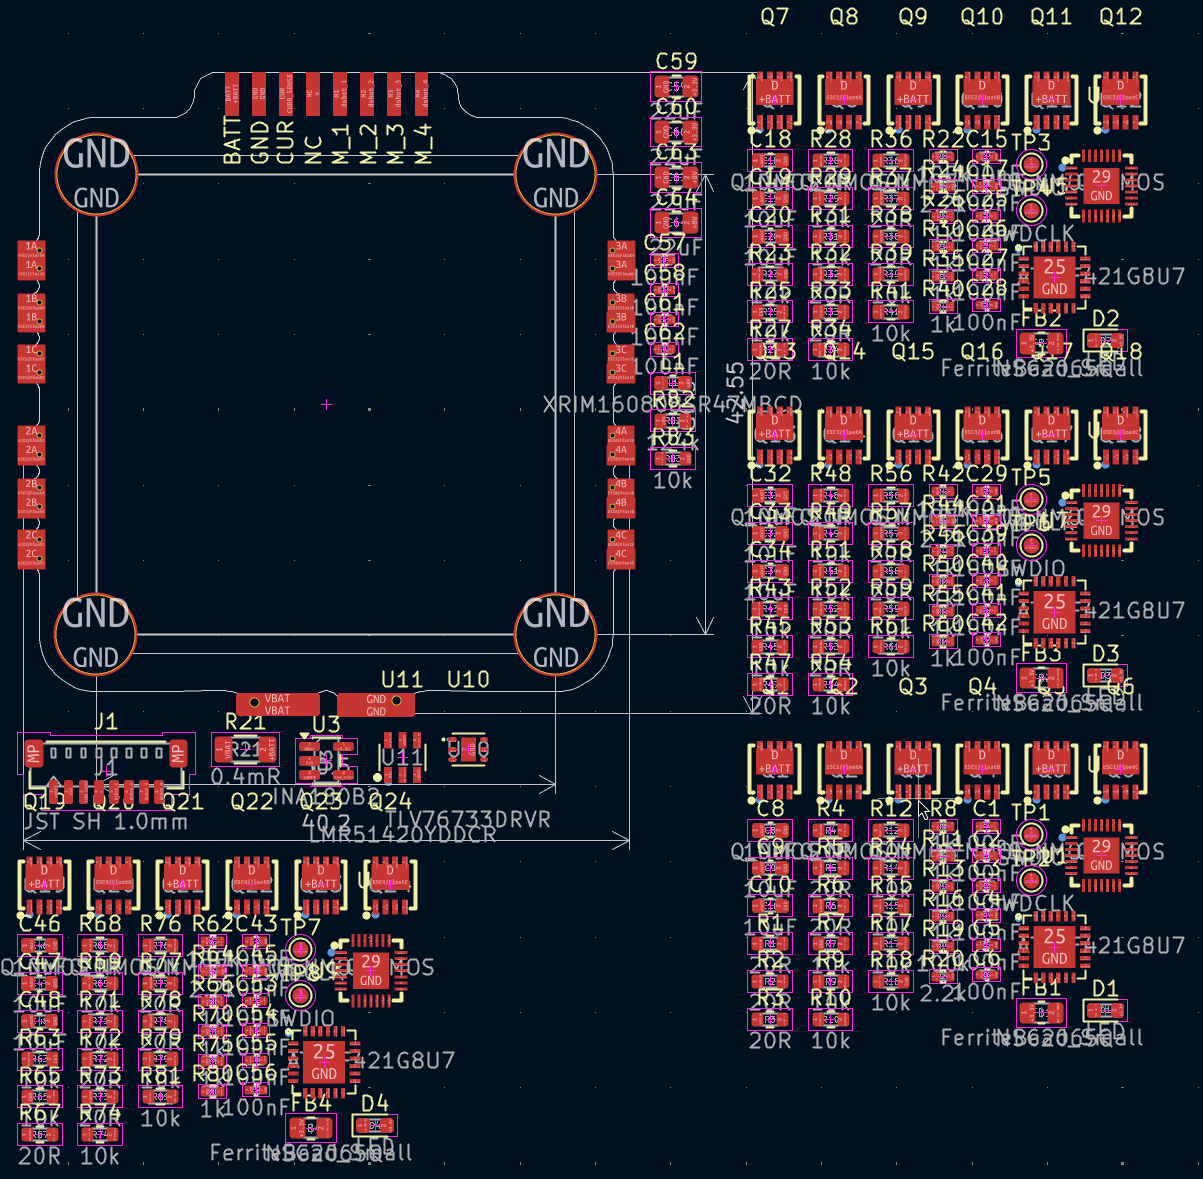
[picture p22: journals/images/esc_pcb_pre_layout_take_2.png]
Board new components


### Board Design

Next I'm going to actually design the ESC board outline around where it needs to go / the frame. This does mean I need to have a look at some frames, and decide which style I'm going with.

After some research, the [BetaFPV Air 65](https://www.aliexpress.com/item/1005009415953442.html) is looking promising. It's cheap, commonly used and even has technical drawings!

This frame uses a 25.5x25.5mm FC mounting design, with M1.4 screws.
This is slightly smaller than my current design (30.5x30.5mm), but the smaller screws will absolutely help (current ones are M3).

---

I've whipped up a quick design for the board outline in onshape, first time using it and its much better than fusion lol. Also my first time doing proper parameterized stuff, and thats quite fun as well. 

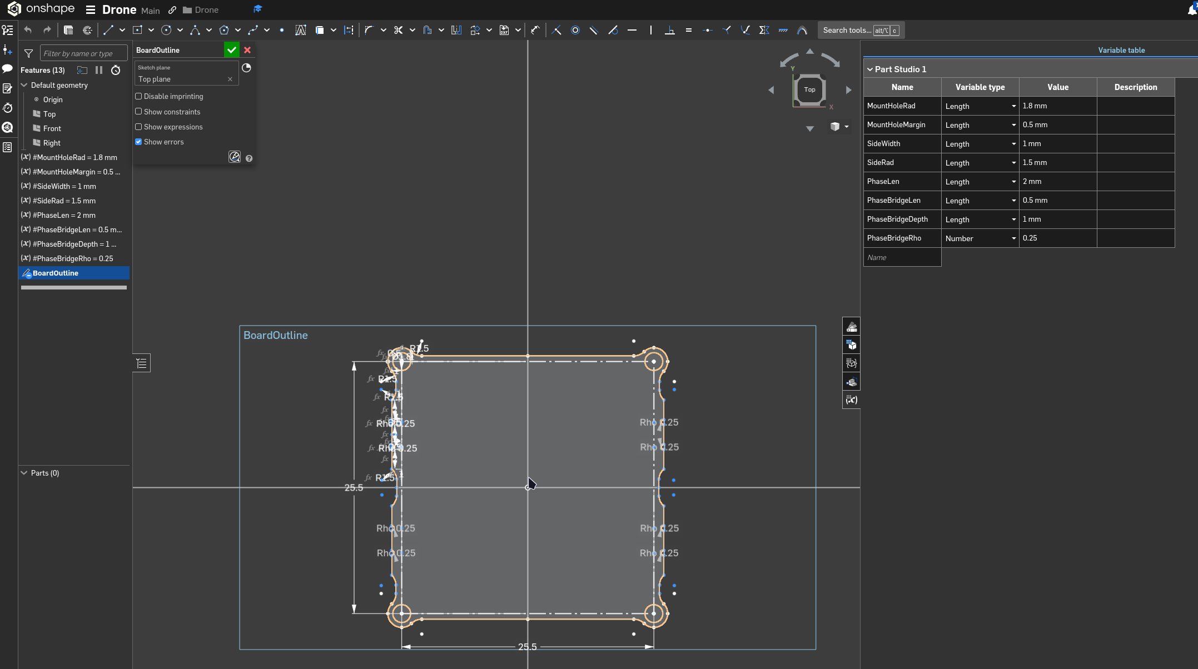
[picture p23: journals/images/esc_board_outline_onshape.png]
Onshape design


Importing it into KiCad, and it is a wee bit smaller than the orignal size, but I'm sure it'll work (i'm not but yknow).

### Layout time

I have made a breakthrough on the layout. Before I was having all the mosfets on the same side of the board, but I can actually have each half of the half bridge on opposite sides of the board, as they both connect via the pads on the edge, which are connected through the board.

I'll pick this up tomorrow and hopefully finish off the layout \:)
G'night!

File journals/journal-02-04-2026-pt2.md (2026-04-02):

# Drone Journal 7 - 02/04/2026 Part 2!

Ello ello ello!
It's been a few hours since the last journal and I've been having a think about this project. I'd really like to set a specific scope for this, and then base my decisions off of that. 

My main problem before was that I had some wishy-washy idea of a 3" drone, but then went and specced my ESC to 165A (like 8-10" drone territory lol), and this was causing a lot of headaches.

I'd really like not to go in this weird in between territory of 3", where its not quite a 5" and not quite a whoop. It makes component sourcing harder and also just design in general: Theres not a lot of 3" drones out there. 

5" Drones are very standard, and theres a ridiculous amount of selection, and some pretty standardized mounting patterns etc... Whoops/Tinywhoops are often a bit less standardized, and have much less of an open source / diy build community than 5", but there is still some stuff available.

The other thing to consider is that whoops require much lower power, typically 10-20A compared to ~80A for a 5" drone. This would simplify design significantly, and certainly make the drone cheaper.

---

## The big decision

Considering the pros and cons, I have decided to go with...
`**drumroll please........**`
A **whoop.**

Clap clap clap, blah blah blah
I chose this because of money, and ease of design, but also because I've been having a loottt of fun in the simulator flying smaller drones, less power but indoor spaces are fun and you can still get quite snappy and responsive movement with them.

---

## Better design specifications

I'm going to organise my design specs into categorys this time, and go into a bit more detail on the hardware requirements entailed by my intended outcome.

### Video
- Analog video transmission
- `>50m` range
- Easy to use receiver (screen w/ desktop compatibility so I can connect to my Oculus later)

###### Hardware
- `25mW` gives `300-800m` range. Go with `100mW` just to be safe.
- Chip that meets spec is TX5823: `<=200mW`
- Receiver will output av signal, need a capture card if I want to parse into computer. No oss solutions I found in 5 mins googling, look into more.

### Audio
Not required, but if I've got space and money could be fun. If it were to happen, these would be the requirements:
- Reasonably listenable audio (not ridiculous crackle / breakup)
- Similar range to VTX
###### Hardware
- Could literally just run audio into the same transmitter chip, should probably work but would need to research more. Just use a different channel which could be annoying if other people flying, defo have a way to disable.

### Control
- Receive ELRS
- Range higher than VTX
###### Hardware
- Use external receiver: XR2 Nano or XR1 2.4Ghz single band.
- Transmitter is what really matters, also buying:
    - T8L is `20-100mW`
    - Pocket is `250mW` I think? 
- Both should be fine

### Battery
- `>5 min` flight time
- Has some power, enough for manoeuvrability
###### Hardware
- Random person on reddit said `4s 450mAh` gave 10min which would weigh like `50g`
- `2s` should be ok for me be good, `>300mAh` should be adequate
- This means needs to handle max of `8.4V` (+margin)

### ESCs
- Won't explode
- Feel responsive
###### Hardware
- What I'm getting from websites is `~12A` should be a good goal to aim for (this is per channel, so `48A total`). This is continous, peak should be `15A / 60A Total`
- Only need to handle `8.4V` (see battery)

### FC
- Integrated VTX (see video)
- Gyro
- Run betaflight \:)
- USB programmable
###### Hardware
- MCU: STM32F405
- IMU: ICM42688
- OSD: MAX7456

### Motors
- same as everything else, responsive, and compatible with esc specs
###### Hardware 
- `1103` / `1102` motors (`10000-11500kv`)
- Tri props, not too high pitch as this will drive up current

### Frame
- Light
- Very durable - I want to crash this thing lol
###### Hardware
- If I decide on carbon fiber, I'll buy a frame, if not, i'll either buy a plastic one or get some tpu and design and build one myself.
- `<80g` frame

---

And I think thats about all \:)
Only other considerations I have are with pcb design and stuff, just keeping in mind proper grounding and isolation of rf stuff.

My next steps are going to be going through the current ESC design and seeing what stuff is overkill, probably respeccing mosfets and gate drivers, and then redesigning with the new specifications in mind.

I guess I should probably stop talking and start doing yknow...

---

### MOSFET Selection

Given an example motor: [Betafpv 1103 11000kv](https://betafpv.com/products/1103-brushless-motors)

| Voltage | Weight |
|---|---|
| 3.7-7.4V | 3.3g |

From [ti mosfet guide](https://www.ti.com/lit/ta/sszt819/sszt819.pdf?ts=1775115429977):
> The 10A-30A space that small battery-powered tools and home appliances occupy is the sweet spot for 5mm-by-6mm QFNs.

Given max `7.4V`, I'm going to aim for `~ >24V` continous V<sub>ds</sub>, which leaves a pretty comfortable amount of headroom for mystery electricity stuff.

Given I need peak currents of `~15A`, I'm going to go out on a limb and say that `20A - 30A` will be good for I<sub>d</sub>.

R<sub>ds</sub> basically determines how hot they'll get, and we can find peak heat losses via the equation:
> P = I<sub>d</sub><sup>2</sup> x R<sub>ds</sub>

The mosfets i'm currently using have an R<sub>ds</sub> of `2.9mΩ@10V` and `4.2mΩ@4.5V`. My drone will be running at `5-7V`, so I'll just take the average of these two numbers, which is `5mΩ@7.25V`. 
Plugging this into the earlier equation gives us
> P = 12<sup>2</sup> x 5*10<sup>-3</sup>
> P = 144 x 0.005
> P = 0.72W

`0.72W` of heat is quite a bit to be honest \:O That's enough to heat 1cm<sup>3</sup> of water by `0.171428571429 °C`
In all seriousness, I have absolutely no clue how much this is, or how much it will effect the mosfets or anything. There definitely will be some air cooling (drones fly) but I'm genuinely unsure as to how big of an issue it is.

###### *A few moments later...*

Yeah I still have no clue and I can't be bothered researching this. I'll just say it'll be fine, I can always slap a fan on if I find out later that its really bad.

For the sake of maths, I'm going to assume that 1w is fine for heat losses (mostly bc it came out with numbers that made some sense)

Such, we can solve for R<sub>ds</sub>:
> R<sub>ds</sub> = P / I<sub>d</sub><sup>2</sup>
> R<sub>ds</sub> = 1 / 144
> R<sub>ds</sub> = ~7mΩ

Thus, I'll try to aim for a bit less than this, probably `<=5mΩ` at whatever my gate driver IC runs at (currently `8V`).

For the gate driver, I reckon I'll just stick with the current one. It's potentially a bit overkill, but it's cheap, easy to use, and I've already got the schematic sorted for it.

That just leaves the mosfet selection! I'm just going to browse through jlcpcb parts for a bit, and see if anything looks particularly good.

---

You know what I'm finding; All of these mosfets in a good range already have the same packages as the mosfets I was already using, and the ones I was already using were just better specced as well, and available from jlcpcb. I might just stick with those \:(

--- 

Alright, so where am I actually going to save space? Well given that I'm aiming for `48A` instead of `165A`, I can use some lower rated components, and now that I'm targeting 2s instead of 4s-6s batteries, I can lower the voltage rating on everything as well, which should significantly help.

I can also shrink the shunt resistor a bit, and decrease the size of the capacitor banks, which were quite massive. Even just reducing the resistors down from 0805 to 0603 or 0402 would be quite life changing.

That might have to be a job for tomorrow though, because I've already spent a bunch of time today, I'm tired, and it was the last day of school... which means that tomorrow I can do a ten hour lock in session \:)

Night folks!

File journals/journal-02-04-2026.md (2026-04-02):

# Drone Journal 6 - 31/03/2026 <-> 02/04/2026

Welp, I haven't given an update in a couple days, mainly because I started my second project on the 31st, but also because my laptop charger finally gave out so I was unable to do any work yesterday. Fortunately, I did end up fixing it but I had to wait until I could go and get some bigger heatshrink, which took a minute.

Anyways, I'm back now and ready to rock! Last day of school for the term for me as well, which is nice; Next few weeks should see massive progress.

## Onto it!

My first order of business today was finishing off the layout of the pcb for the ESCs. I was extremely worried about everything fitting, but after shuffling some things around, I've squeezed it all in \:)

It might be quite a pain to route though, but given I've got 4 layers to work with, I'm sure I can make it happen.

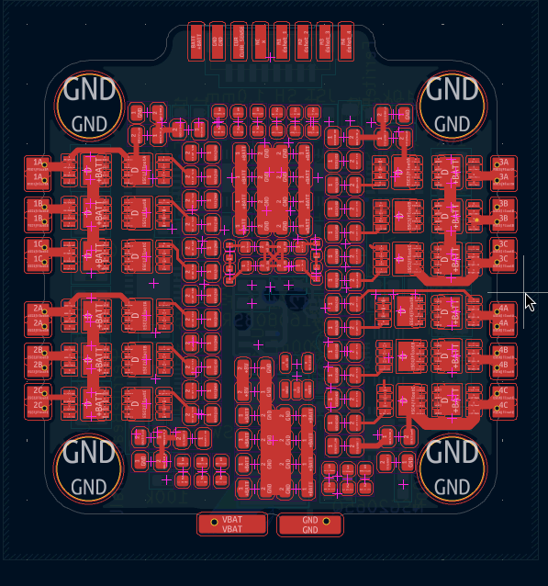
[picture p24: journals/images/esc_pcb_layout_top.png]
ESC Full layout top side

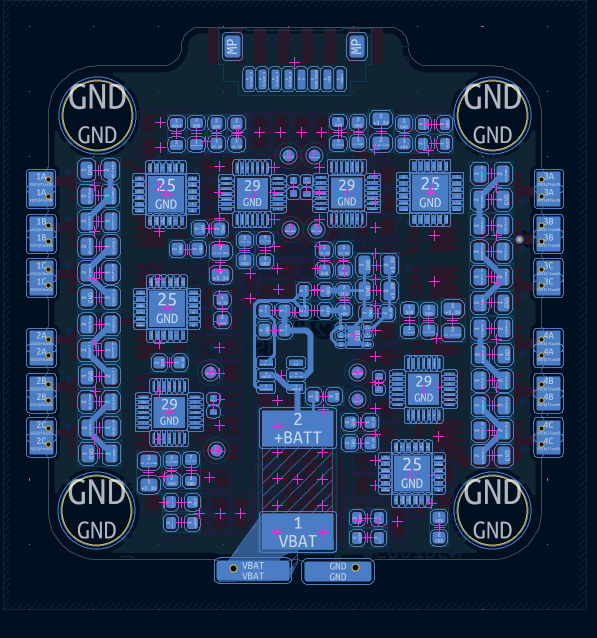
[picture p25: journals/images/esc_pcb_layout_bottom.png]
ESC Full layout bottom side


I'm considering getting two side pcba, because it all looks like hell to solder. If its too expensive, I can probably solder up on side, but I'm not sure if I'd do the top or bottom.

However, those problems are for future me, for now: Routing!

---

Hmmm, I have bad news...
This layout is not really gonna work \:(
In short, not only is everything really tightly jammed, but I've not really considered a lot of the routing of high power stuff, and I'm not very confident that things wouldn't just go up in a pile of smoke. I think I'm going to make a few changes and see about doing a slightly better design.

My first thing will probably be to just increase the size of the board a little. Instead of 30.5x30.5, I'll go to a 40x40/Φ3mm design. Which should give me a lot more flexibility in layout and routing. I'll also probably try to get some smaller components, and finally I'm also going to use a 6 layer pcb, which will absolutely help with power handling.

It could also be an option to go with 4 seperate ESC's instead of one main board, but this imposes additional challenges with power distribution, albeit different ones.

I'm going to put the redo of the layout and component selection on a different journal, so look out for edition 7 soon \:)

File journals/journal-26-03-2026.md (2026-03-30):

# Drone Journal 2 - 26/03/2026

Onto speccing some stuff!
##### The first major choice is the MCU. 
I'm not going to be doing anything special, so I've elected to go with the common choice of a STM32F405. Should be able to handle all my needs \:)

##### Next, a gyro / IMU.
<s>Again, going for the easiest choice, I'll take an MPU6000. They're tried and tested and cheaply available, even if they are a bit old.</s>
Nevermind I'm using the ICM42688, because it's available on jlcpcb parts lol

##### OSD 
To overlay the osd, a MAX7456 is typically used, and I see no reason to deviate from this.

##### Barometer
If I were to have a barometer, I'd use the BMP280, again just going with super common choices. However, because they cost 6 bucks each, I think I'll pass on them for now, especially given that its not necessary for anything other than osd stuff.

##### GPS
Honestly, GPS sounds like a total headache, and I'm not sure how relevant it'll be to this project, so I've decided to just skip it.

##### VTX
<s>
I'm wanting something cheap for the vtx, which limits my options a lot (while not going into crappy clones), but I think I've somewhat narrowed it down to the SpeedyBee TX800, which is available for ~35 USD, which is much better than other options. For some reason its more on aliexpress than the official site, so I'll need to do some research over where to get it.

I could also use the SpeedyBee TX500, which is a smaller, lower power transmitter designed more for micro drones, which is somewhat in the size class I'm looking to build. It is also cheaper so this may be a decent option.</s>

TBS Unify Pro32 Nano 5G8 is cheaper and available in NZ

For receiving the signal, a decent option I reckon would be a [RC832](https://www.getfpv.com/5-8ghz-48ch-fpv-av-receiver-rc832.html) receiver coupled with an analog video to usb adaptor, to bring it into my laptop and potentially output to my vr headset I already have, instead of buying fpv goggles (\$\$\$)
Even still, it's gonna be another 25 USD \:(

##### Camera
<s>I'll probably just go for generic aliexpress no brand camera, but ideally I'm looking for one with ~115° FOV, </s>
The caddx cameras are looking like a decent option, and if I were to go with them I don't need to worry about osd on board (although I probably would still want it, for compatibility with other cameras and controllability via betaflight). I'll keep looking but I can't really find any cheap ones on aliexpress.

*Note: kiwiquads is local and has cheap cameras and cheap shipping (30 NZ + 5 NZ shipping)*

##### Batteries

These are all quite generic, so any specific one will do later, but I'm going to put a bit of thought into my desired battery and flight time now.

I'd ideally want ~2-3 minutes of flight time, and so if I can get my drone weight (incl. batteries) to around 300g, then I'll want around 450mAh at 7.6v nominal, for which there are a bunch of good options.

##### Tx / Rx
For a transmitter / controller, I've decided to go with a Radiomaster Pocket / Crush, which is pretty much the cheapest you can get lol. For receiving, I've elected to go with a RP1 v2 also from Radiomaster. It's cheap and it'll work, thats about it \:)

Moneys:
RM Pocket: ~60 USD
RP1 v2: ~20 USD
Caddx Ant: ~20 USD
TBS Unify Pro32 Nano 5G8: ~35 USD
VRX: ~20 USD
FC: ~20 USD probs
Frame: ~5 USD probs

Total: ~180 USD
Add 60 USD because shipping + extra bits I haven't thought of etc...
~240 USD

AAAAHHHHHH THIS IS SO EXPENSIVE \:(

I might have to do some rejiggering and see about absolute cheapest thingies.

god theres not a lot you can do \:(

Ok, well, to wrap up what I've done today, it's basically been a lot more research into specific parts I can use, and how to optimise cost (yikes). Overall, I will say its not looking promising. I've also asked on slack to clarify whether I can buy a controller with the project money, which'll pretty much determine the fate of this project lol, wish me luck \:)

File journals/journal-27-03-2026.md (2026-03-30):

# Drone Journal 3 - 27/03/2026 <-> 28/03/2026

Alrighty; Much more research has been done and I have nothing but good news!

First of all, I've received clarification on my questions on slack, and it seems I am allowed to buy supporting hardware (providing I optimise for cost) and I also should be good with designing stuff.

Secondly, I've found some very very nice resources on how to build diy ESC's and VTX's, which should hopefully save a loottt of money, being a single aio board instead of a bunch of seperate components.

So yeah! I suppose we should just get into it.

##### VTX / VRX
VTX will be done using the TX5823 chip, which is a nice little IC which handles all the tricky things for me. It transmits at ~200mw on the 5.8Ghz band, which is perfectly usable for me. Most VTX's are around 500-1000mw, but 200mw should be fine for my use case. As low as 50mw can give around 50-100m range, and so mine should be around double the range (from the inverse square law).

For receiving, I'll be using the RX5808 chip, which is very popular among diy receivers. There's also some open source hardware and software available, which will be greatly beneficial when designing my own version.

##### ESC's

Again this is still sitting at a maybe for me. I've found a few resources online on how to design one, but it'd probably not support dshot (needed for motor telemetry) and I'd be kinda worried working with such high power devices (eg things would probably blow up).

I'm going to leave this as a maybe for now, and get started on what is going to be on my flight controller.

##### Batteries
In order to spec a battery protector, I need to know what type of batteries I'll be using. 

## Flight Controller Speccing

- MCU : STM32F405
- IMU : ICM42688
- OSD : MAX7456
- VTX : TX5823
- ESC : Generic 4 in 1 DShot compatible
- Battery Management chip : blahblahblah

Ok enough research yap I'm itching to get started. Making my own esc because I saw a schematic online and it looked easy as hell so yknow, yolo!

Straight into kicad I go \:)

Alrighty, I'm pretty much just copying the datasheet and another example project right now, and for future reference I'm going to give a bit of an explanation of my understanding of how shit works.

First of all, for one esc, we need to switch to have three 'modes' for each coil(?) of the motor. Basically it needs to switch between high, low, and floating. High pulls the stator towards, low pushes away (i don't really know but ya get the idea). when floating, the coil acts as a generator, and you can measure the voltage (back emf) to get the speed of the motor.

The mosfets are too big to be switched by a mcu directly, and theres some other shenigans wherein the set of mosfets to switch a coil to high require higher voltage than the source which means that we'll use a motor **gate** driver ic. (gate being the transistor gate, don't get confused future me lol). 

There are logic inputs for low, logic inputs for high, and then their respective outputs, for each phase. Alongside this, there are VB pins and VS pins, which are for the bootstrapping (eg boosting the voltage at the gate of the mosfet). These need a capacitor which will be charged when the driver is low, and then discharged when logic goes high in order to properly drive the mosfet. To see how to pick the value look at the first 5-6 pages [here](https://www.ti.com/lit/an/slua887a/slua887a.pdf?ts=1774680750455).

For others developing an ESC, heres some amazing links:
- https://wiki.am32.ca/development/Hardware-Design.html
- https://www.youtube.com/watch?v=TwAmmPxOpTM
- https://www.ti.com/lit/an/slua887a/slua887a.pdf

For the esc mcu's, I've decided to go with the AT32F421, pretty much just because it's the cheapest option.

Alrighty, I've done quite a good amount of work for tonight, most of the esc is done, I just need to work out what telemetry / monitoring I want on it and then wire up four of them into one board. It's pretty much a case of whether I want voltage / current sensing on the ESC or on the FC, and I'm not really sure whats typical / best practices. Anyways, im off to bed now, as its a bit past midnight and I need to get up early tomorrow \:)

Feeling much more confident about this project overall now, might not even take too long to finish up \:O

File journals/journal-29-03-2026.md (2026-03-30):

# Drone Journal 4 - 29/03/2026

It's still esc time busters!
Getting straight back into schematic work, just need to finish wiring up the MCU and then sort out other stuff.

Ok some notes for future me again!
Current sensing is done by a current sense amplifier, wherein you add a very small shunt resistor, which induces a voltage drop, and then multiply the voltage drop by the amplifier gain, and then measure that voltage via an adc on a mcu to get the current.

I'm using a 50v/v gain amplifier, and we need to keep the voltage on the adc <= 3.3v
```
V=IR * GAIN
```
So given a constant V (3.3), we can choose a desired max current and then solve for the resistor size.
```
R= V / (I*GAIN)
```

For a max current of let's say, 100 amps, we would need a 0.66mΩ resistor.
Looking at the jlcpcb basic parts, the smallest resistor is 100mΩ, which would give us... 0.66A of max current \:(

<s>Oh welp, extended parts it is.</s> So it turns out jlcpcb doesn't stock any small enough resistors, so I'll just need to buy my own.

I'm going to go with a 0.3mΩ resistor, which will give a max current of 220A, and need a power dissipation of ~10W.

Alrighty, now thats all wired up, it's time to move onto getting the voltages we need, which are 3.3v and 8v. Fortunately, I can steal a bit of circuitry from the reference, but I'll need to get the 8v regulation myself.

I've opted for the LMR51420 chip, which is designed for taking in battery power pretty much. It does have a range of 4.5v - 36v however, which means that 1s batteries are off the table. I was always planning to use 2-4s batteries, so there shouldn't be any problems. 

Ok, I've tidied up the schematic a bit and it's looking pretty good! Theres some drc errors but I'm pretty sure they're all ok, just crappy symbols from the lcsc tool.
Anyways, heres the schematic as of now \:)

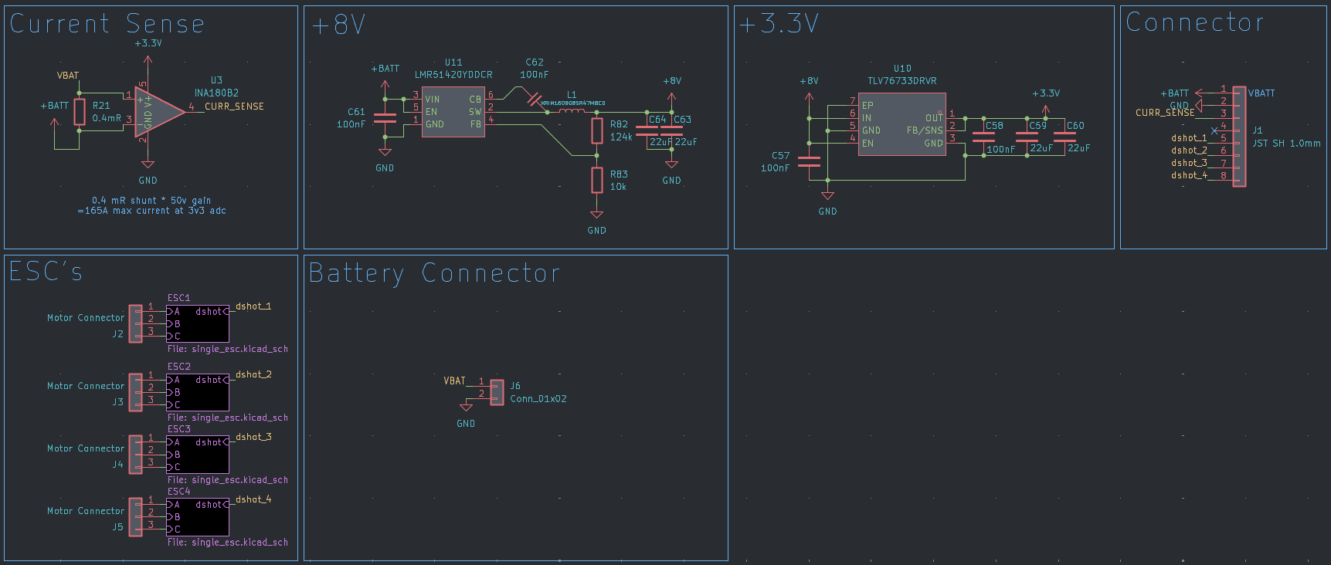
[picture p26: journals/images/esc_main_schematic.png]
ESC Main Schematic

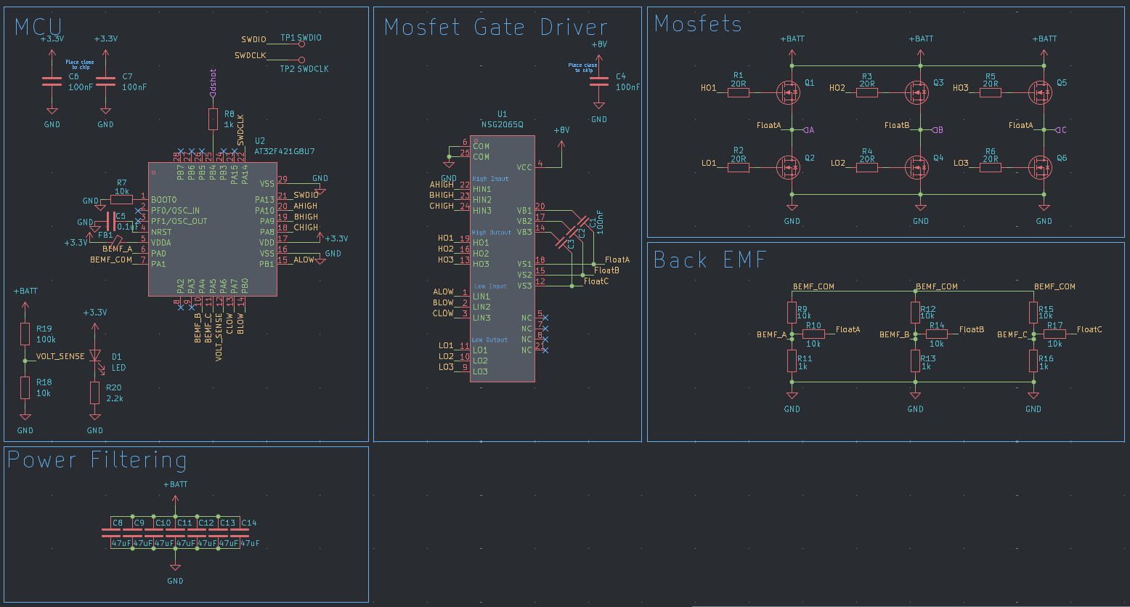
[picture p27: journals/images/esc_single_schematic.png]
ESC Single Schematic


Now it's time to sort out my bom and get footprints done \:)

---

Ok, I've hit my first hurdle when specing components. For basic parts, the highest voltage 47uF caps JLCPCB offers are 10V, which would limit me to a 2s battery. I think I'll go with this for now, but I might change it in the future.

---

Welp that took longer than I thought it would, but I've finished it now. I don't need to spec a few of the components because they'll just be solderable pads on the board (specifically the motor outputs and battery connector). This is looking to be a wee bit expensive though \:( 
Oh well, what can ya do.

Now that's done, I can get cracking on assigning all my footprints in KiCad, but after that, I reckon I'll head to bed, getting a bit late and I'm kinda tired lol.

---

Done! Well, the pcb's looking kinda scary to lay out lol:
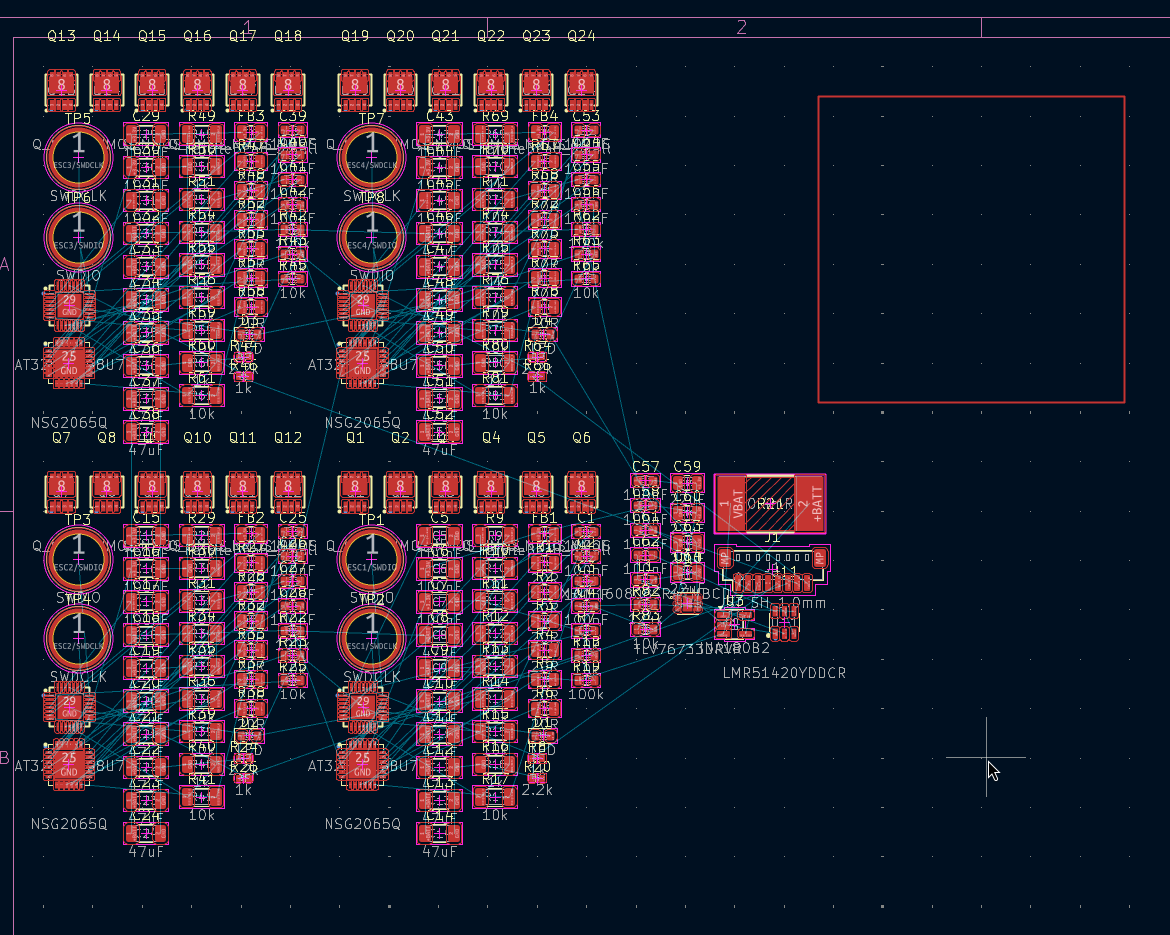
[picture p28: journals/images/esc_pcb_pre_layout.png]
PCB Pre layout

Not a job for today though! Goodnight peoples \:)

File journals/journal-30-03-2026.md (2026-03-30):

# Drone Journal 5 - 29/03/2026

Welcome back to drone day 5! 

Today was a pretty chill day, I made the choice to swap a bunch of components to lower power rated versions, just to decrease the size a little bit. I think that most of the time, currents will low enough that it shouldn't matter, and high currents *should* only be momentary. Hopefully its fine, only time will tell. Other than that, I started work on the layout and routing. I sorted out the main footprint for the board, and have layed out and routed a bunch of stuff, but in all honesty I'm doubting it will fit. I'm going to go through and see where I can shrink / cut components, or maybe do better layout. If all else fails, I can increase the size of the esc, but this would be a bit unfortunate, as they are made to a roughly standard size and I would love to stick with that for compatibilities sake. Potentially I'll spec down the esc to a lower max rating, which could help the size a lot.

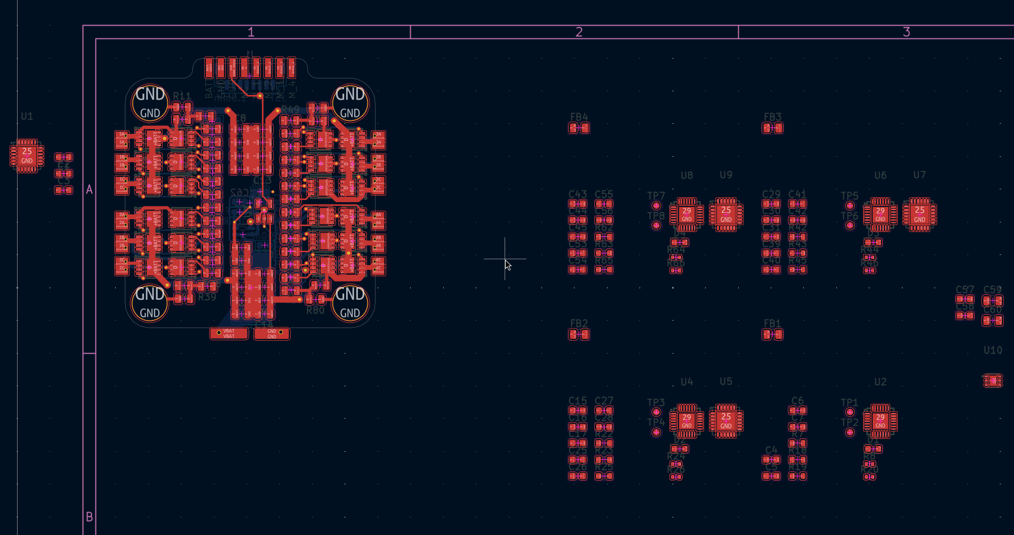
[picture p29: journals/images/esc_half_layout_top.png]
ESC Layout top side

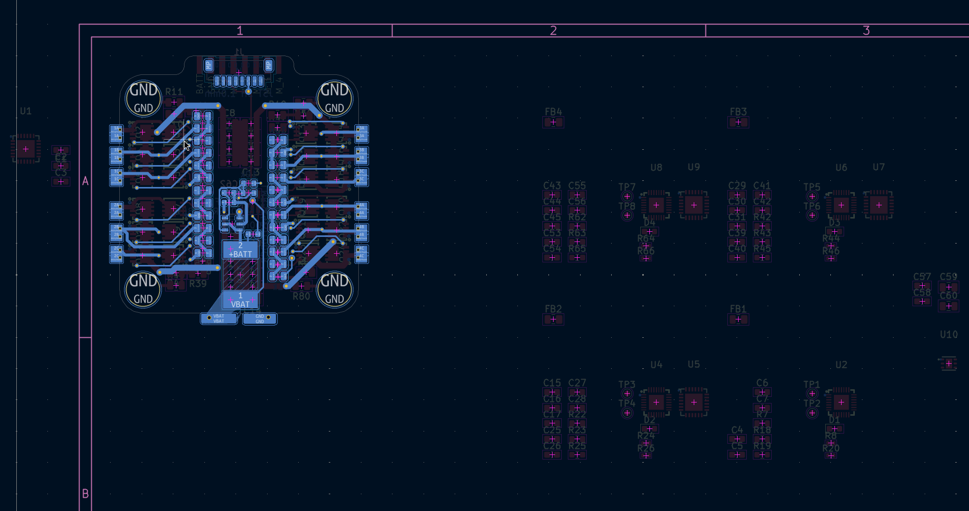
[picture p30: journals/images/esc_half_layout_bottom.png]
ESC Layout bottom side


Bis morgen!

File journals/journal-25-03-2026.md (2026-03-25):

# Drone Journal 1 - 25/03/2026

##### 'Ello folks! 
The beginning of a new project, truly a momentous occasion \:)
I've recently been getting a wee bit into fpv drone flying (just in sims as of yet), but I'm deeply enjoying and am looking to do a little irl piloting. I've been wanting to make some ROV for a while now, but have been tossing up between a plane, boat, drone, or underwater rov. Given the relative accessibility of drones (with a bunch of nice software written, and a loott of hobbyist components available), and also my recent interest in them coinciding with this program, I've decided to gun it and just give it my best shot. 

---

So, getting straight into it; What does a drone actually need?
| What | Why | Buy? |
|---|---|---|
| **Frame** | Holds the other components in place (duh); |  O |
| **Motors** | Yeah i think you know what these do lol; |  X |
| **Props** | Attach to the motors, probs a bit useful; |  X |
| **ESC's** | Motor drivers: Required for 3 phase and also control motor speed;|  ? |
| **Flight Controller** | The big brain, majority of this project; |  O |
| **Battery/ies** | Power, might not make these myself; |  X |
| **Sensors** | Baro, Gyro, Compass, Accelerometer, think thats most of 'em; |  O |
| **GPS Module** | Not strictly required, good for navigation if wanting auto mode; |  - |
| **Camera** | It's a camera, what more could you want :shrug: |  X |
| **VTX Module** | Transmits video from the camera back to the controller / goggles;|  X |
| **Tx / Rx** | Receiving antennae and transmitting, for control and video; |  X |

<sub><sub><sub><sub>ai slop articles are absolutely despicable i hate all of you</sub></sub></sub></sub>

---

##### Alrighty, I'm pretty sure thats a reasonably comprehensive list (excl. a controller + goggles).
Most of this I'll look to buy, but a few things I reckon I can take a crack at myself.

I'll most definitely design a frame, as this is pretty much the main thing that determines a drone's performance and durability, and so just buying one would kinda defeat the whole point of the project.
Alongside this, I will also make my own custom flight controller, for similar reasons. Sensors will likely just be mounted on the flight controller, so don't need to buy those seperately.

I think that I potentially could design my own ESC's, but I am definitely not as confident in my skills in this area, as it deals with much more of the physics side of electronics than the computer side, and I am not super familiar with how to work in that area. I'll do a bit of preliminary research but overall I think it's unlikely to happen. ESC's are also not a massively important or unique part of a drone, pretty much all of them are the same so I won't miss out on any creativity and will likely save costs as well.

I also don't feel confident making a VTX, as not only is it a highly complex field (radio transmission), theres also not nearly as much information on how to design one and the best practices around it.

---

## Flight Controller

I've been having a look at the flight controller guided project for blueprint, and it has some pure gold! So here, I'm pretty much just going to copy over some of the planning stage from that to help get my thoughts straight.

#### Feature Definition:
What does my flight controller need to do? What capabilities and what connections?
My drone will be pretty basic, no fancy features and just good ol' classic fpv control, so I might see about any prebuilt solutions for code or something else to scaffold off of, and perhaps have my own seperate (crappy) firmware just for fun. The only thing slightly out of the ordinary I'd like to do is collect telemetry as well as transmit it, so in the case of connection loss or other extenuating circumstances I can analyse the data post flight.

- Powerable by battery
- Control four ESC's
- Receive input from radio receiver
- Get rotation, speed, and altitude data
- Persistently store data even on power off
- Water-proofable
- Programmable via usb
- Low-latency analog video capable
- Tough (i will crash a loottt)

I've very easily narrowed down my choice of software to Betaflight (i almost certainly will want a 'good' firmware, but maybe also my crappy one): It's got a very wide user base, has good support for a variety of hardware and has all the features I could possibly need. 
This does narrow down my choices of hardware for sensors and the like.

OK SCATTERBRAIN TIME BECAUSE I'M RESEARCHING (sorry journal readers this is how it goes)
- VTX is often integrated into flight controllers
- Analogue over digital -> Way better support
- ExpressLRS - something about channel swapping, need to read more to understand
- OpenVTX - thingy for managed channels / bands, defo use (if not using the expresslrs thing)
- use an esc which supports dshot (for rotor telemetry etc)

```
You have most likely seen something like "F4", "F7", or maybe further specified as "F411", "F405", and "F722". These are designations for the different MCU lines. They vary in flash size, RAM, and clock speed. Generally, the higher the number, the more powerful the MCU is.

In order of power, from least to most:

    STM32F411 - Very common in budget and/or AIO FCs due to its low cost and small size. But it's not that powerful compared to most other MCUs
    STM32G473 - A newer option from STM, it's a bit more powerful than the F411, but not as developed and established
    STM32F405 - Pretty much the most common option, it's a good balance of power and cost, being in use for a long time
    AT32F435 - ArteryTek's new alternative to the F405, directly pin-compatible, but with a bit more power
    STM32F722 - Very popular high-end option, but it has a limited flash size. This is not much of a problem nowadays with the Cloud Build system which allows a lot of space saving
    STM32F745 - Somewhat more powerful than the F722, but with more available flash space make it a good option for high-end builds without going overboard
    STM32H743 - The most powerful (and expensive) option. It's not really needed for most builds, but it's a good option if you want to go all out
```
- ok u actually need camera running through fc for osd, so thats defo happening
- acro and 3d only need gyro, accel is for other modes, but probs have anyway just for telemetry
- Baro is only used for gps landing assist in betaflight atm, maybe more in future, but probs not needed (would be nice just for piloting though, although then i think i need gps in order to get land height (baro is from sea level))
- could have a compass if wanted, only use i could see is for planning flights (in terms of flight zones and aviation rules)
- GPS post crash could be handy \:)
- RM transmitter, cheapest would probs be ~100 bucks - ouch \:(
- Will need a vtx chip probs
- Want kinda little one, 2-3"
- would like bi-directional esc's (Not strict requirement)

#### LINKS
https://www.betaflight.com/docs/development/manufacturer/manufacturer-design-guidelines
https://www.betaflight.com/docs/wiki/getting-started/hardware
https://www.betaflight.com/
https://flying-rabbit-fpv.com/2020/10/06/designing-my-own-flight-controller/
https://blueprint.hackclub.com/starter-projects/flightcontroller
https://www.betaflight.com/docs/development/Flight-Controller-Design
https://github.com/anlgncr/custom-betaflight-board/tree/main

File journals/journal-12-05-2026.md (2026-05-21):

# Drone Journal 29 - 12/05/2026

Welp today I've pretty much just been doing more blender work. I re-did all the stuff I lost yesterday (saving regularly this time lol) and am just doing a wee test render. I've decided to go with a cool fisheye style one, just cause its pretty suitable for an fpv drone and it should also fit the zine format well, I can just chuck a circular image in the center :)

Ended up just modelling my desk pretty much, reasonably accurate but I didn't want to hand model stuff so I made do with blenderkit assets.

Heres the render:
render
Low res because I didn't want to wait a year to render but I'll do a better one later.

And with a bit of compositing:
Composited

And then with slightly better framing lol:
Framed

Reasonably happy with this, a wee bit more work to do but unfortunately that'll have to wait till tomorrow. Need to sleep :)

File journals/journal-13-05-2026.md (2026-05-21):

# Drone Journal 30 - 13/05/2026

More blender work today, I've got the first render done which is nice:
Render 1

Second one is gonna be another transparent background one, with some grease pencil stuff.
First though, gotta pick a wee color scheme. The last one I went with rose pine moon because I daily drive that, but I reckon I'll do something different this time :)

Decided to go with gruvbox because it looks fun :)
Gruvbox theme
Nice and pastel which i like.

And with some squiggly bits added in :
Squiggly

And yet more scribbles:
Scribbles

and that gives this as the full render:
Render

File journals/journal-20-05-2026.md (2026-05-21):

# Drone Journal 33 - 20/05/2026

I've just realised I'm yet to figure out a solution for video receiving, and looking at the rx5808 chip, basically the receiving equivalent of the tx5823 chip, its a very similar story. It'll be around 25USD at the cheapest, but in this case unfortunately, theres not really any other options to buy that don't need a pair of goggles.

There is the option of digital transmission, but this isn't really likely to be any cheaper and is also going to be much more complicated. I do reckon I'd like to try out designing a custom vtx vrx stack at some point but unfortunately that is far beyond the scope of this project, as it in itself will likely need several iterations already even without the added complexity of rf electronics.

---

Its the next day now but I'm getting back in the swing of things :)

Again for vrx I do think the best option will be the rx5808 or some other cheap receiver, so I'll go with that for now.

Next up, some actual work lol.
I'm gonna work some more on the firmware and then keep drafting up the readme.

---

Annd a wee bit of fiddling with keil later, I've given up and decided to just use github actions, which worked second try (the filename was too long the first time lol):
Compiled!

Now just to figure out where the actual binaries are stored lol

---

And a wee minute later and after eating, I have all the ESC firmware done and compiled :)

Next up, betaflight :)

Took a hot minute but after some setup and a looot of compiling (note to self, git on wsl is verry verry slow), I now have the compiled betaflight for my target :)

Not really any pictures sorry bc its just a file but y'know :)

---

Just realised I did it from the alpha branch of betaflight but whatever, it should be fine right?

And with that all the firmware is done :)

---

Finally, I did a bunch more work on the readme and have got it to a pretty reasonable state. Still a few more things to do but the project is rapidly approaching the finish line. For future me's sake, heres the todo list:
- [ ] Replace placeholder renders 
- [ ] Add BOM 
- [ ] Add Zine Page
- [ ] Replace main render with different color scheme

Alongside that theres obviously a couple things to polish up for the actual submission, namely making a zine and updating the bom's. God I'm not looking forward to the cost of this project lol.

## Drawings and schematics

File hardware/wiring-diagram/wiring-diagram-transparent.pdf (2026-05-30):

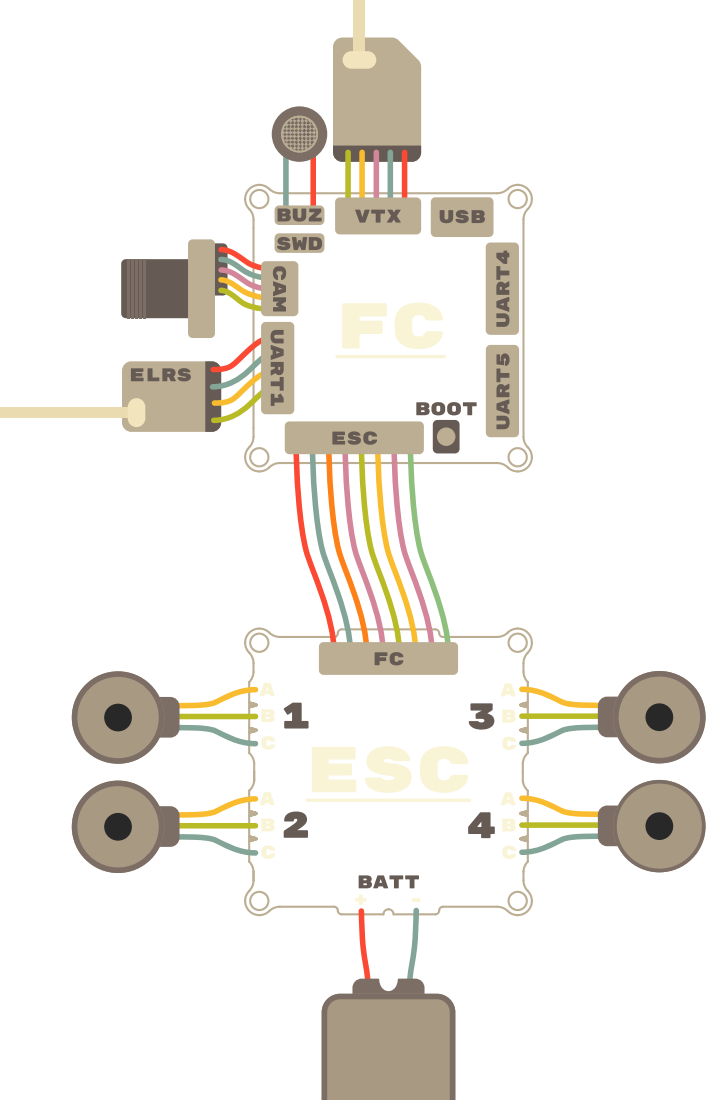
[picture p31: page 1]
ELRS; UART1; BUZ; SWD CAM; VTX; USB; UART4; ESC; BOOT; UART5; Batt

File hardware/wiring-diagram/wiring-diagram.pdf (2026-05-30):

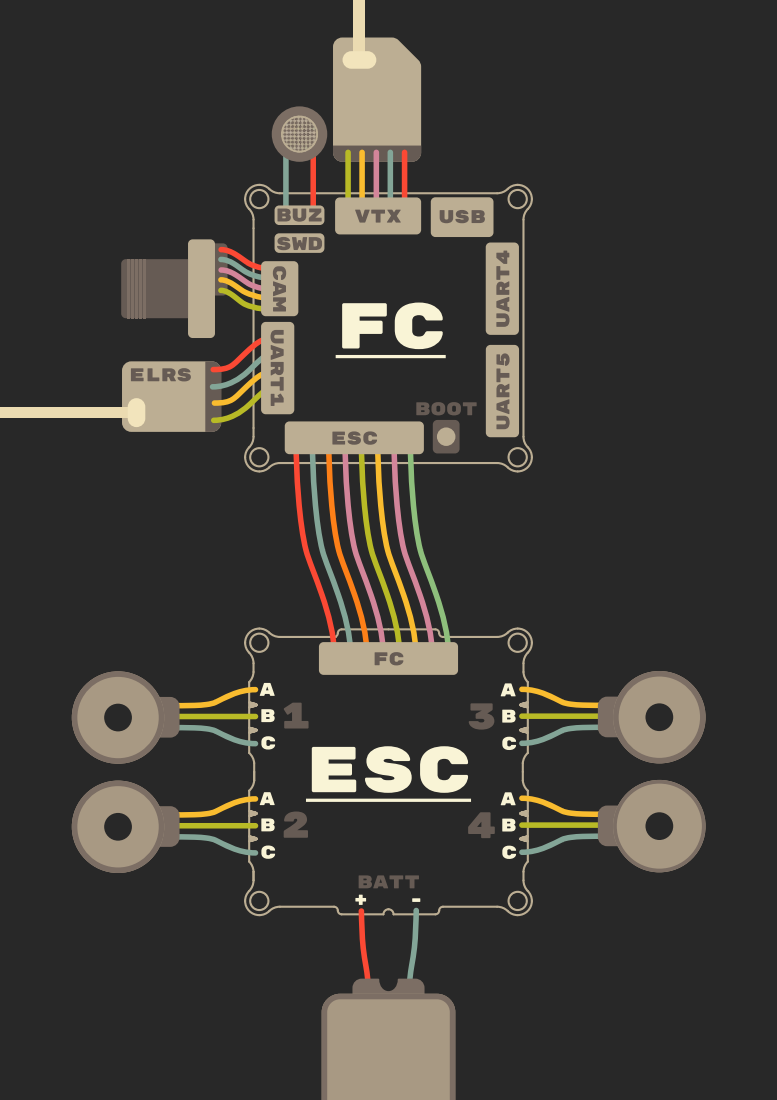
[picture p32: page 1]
ELRS; UART1; BUZ; SWD CAM; VTX; USB; UART4; ESC; BOOT; UART5; Batt

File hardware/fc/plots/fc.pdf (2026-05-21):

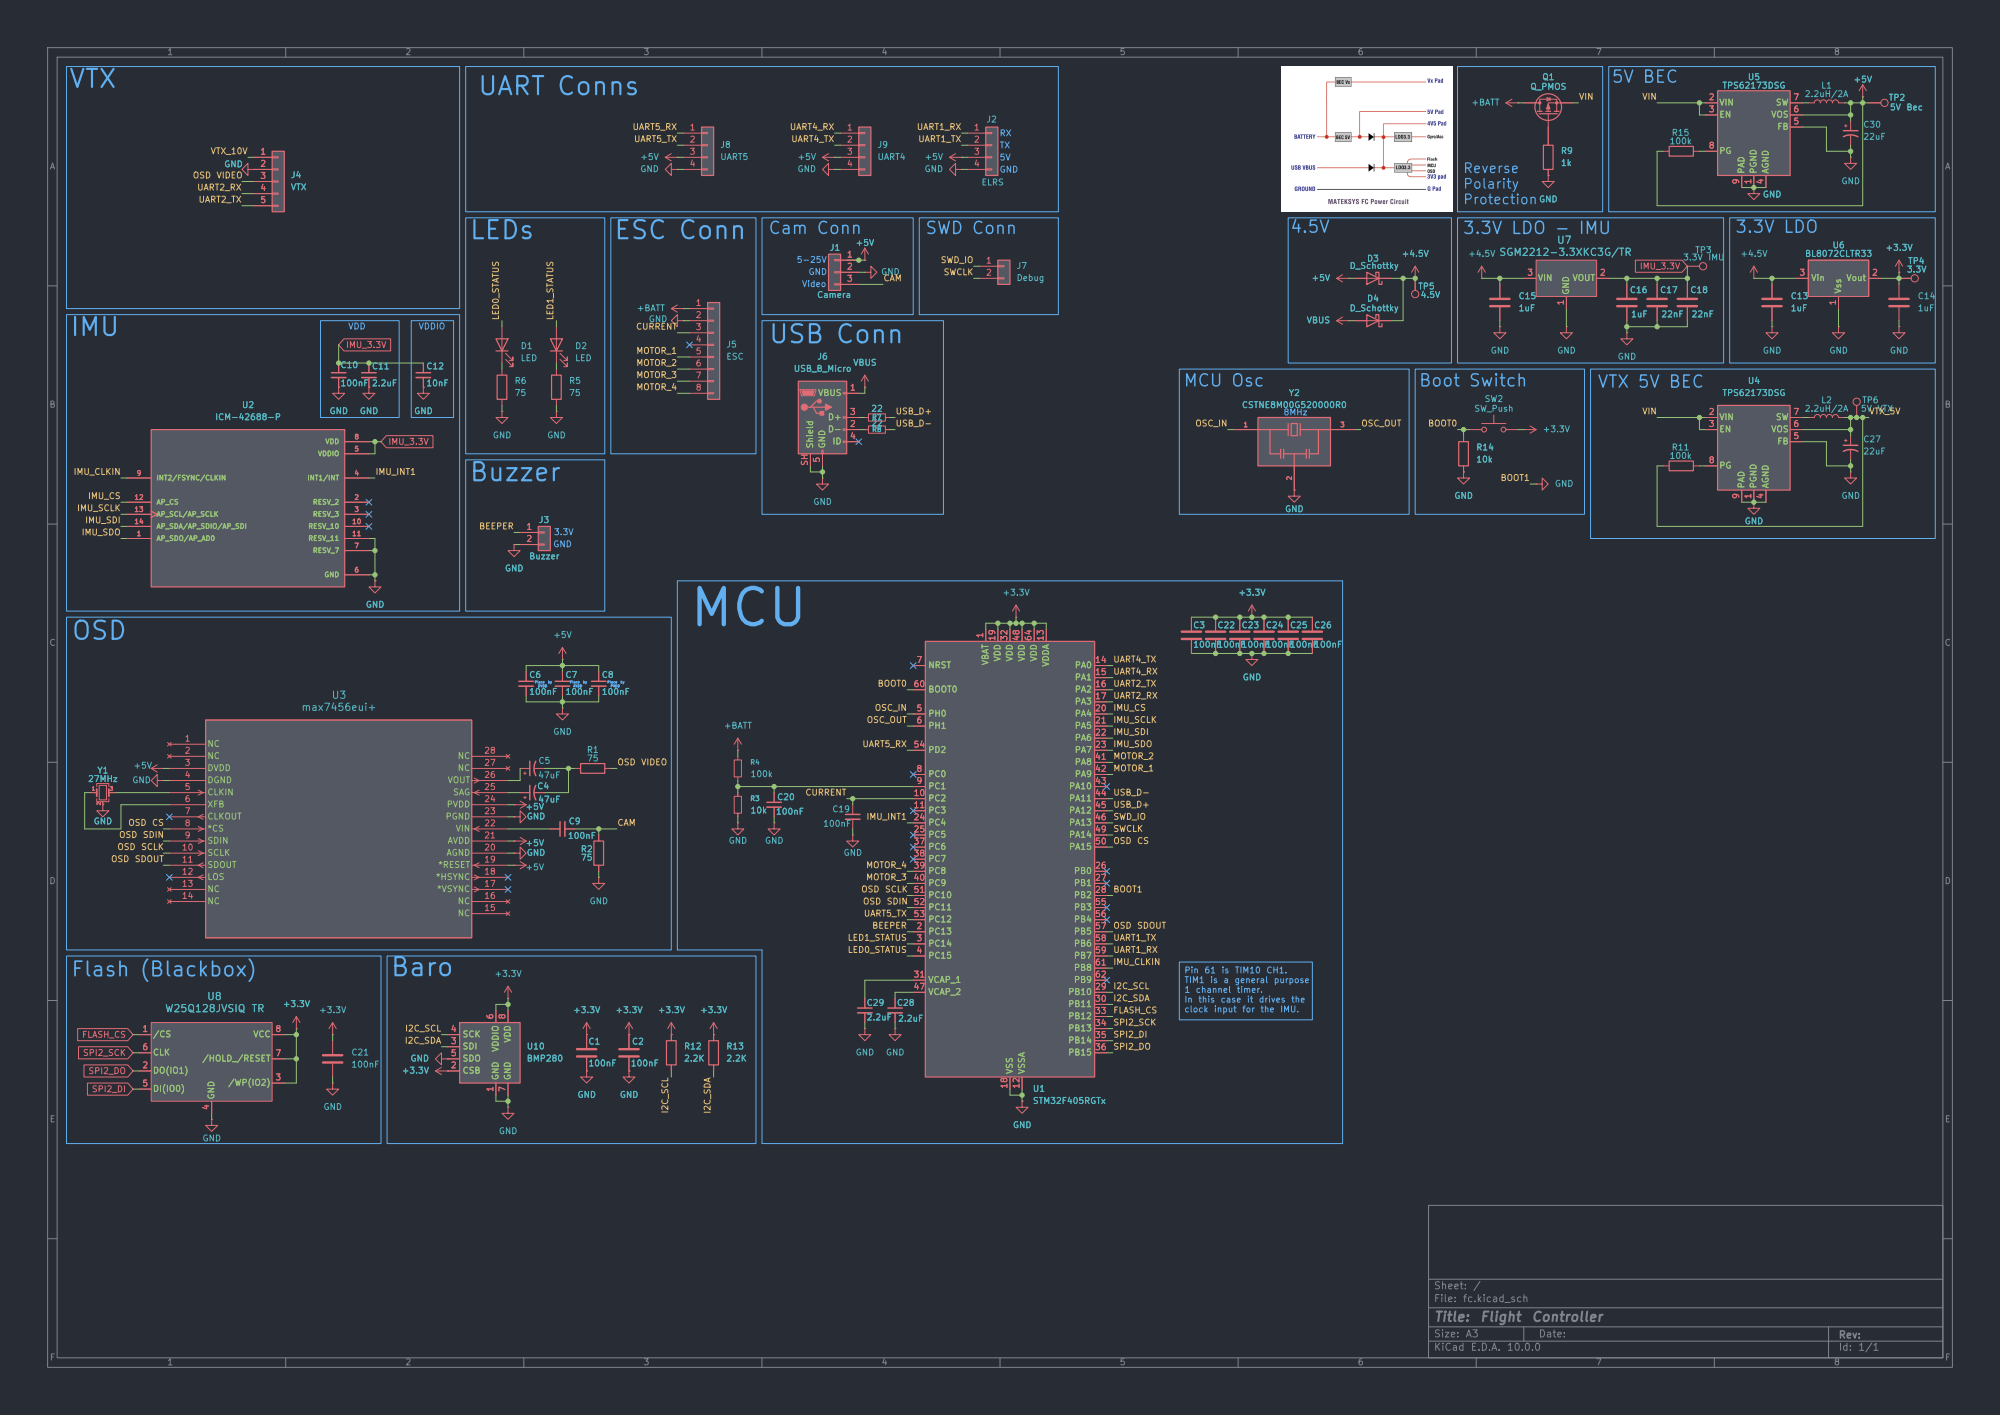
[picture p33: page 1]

3.3V Buzzer

Place by DVDD OSD

Place by PVDD Baro

LED1_STATUS OSD SCLK OSD SDIN MOTOR_3

In this case it drives the

Size: A3 | Rev: | F Date:
KiCad E.D.A. 10.0.0 | Id: 1/1

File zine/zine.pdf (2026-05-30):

# F~ish PV

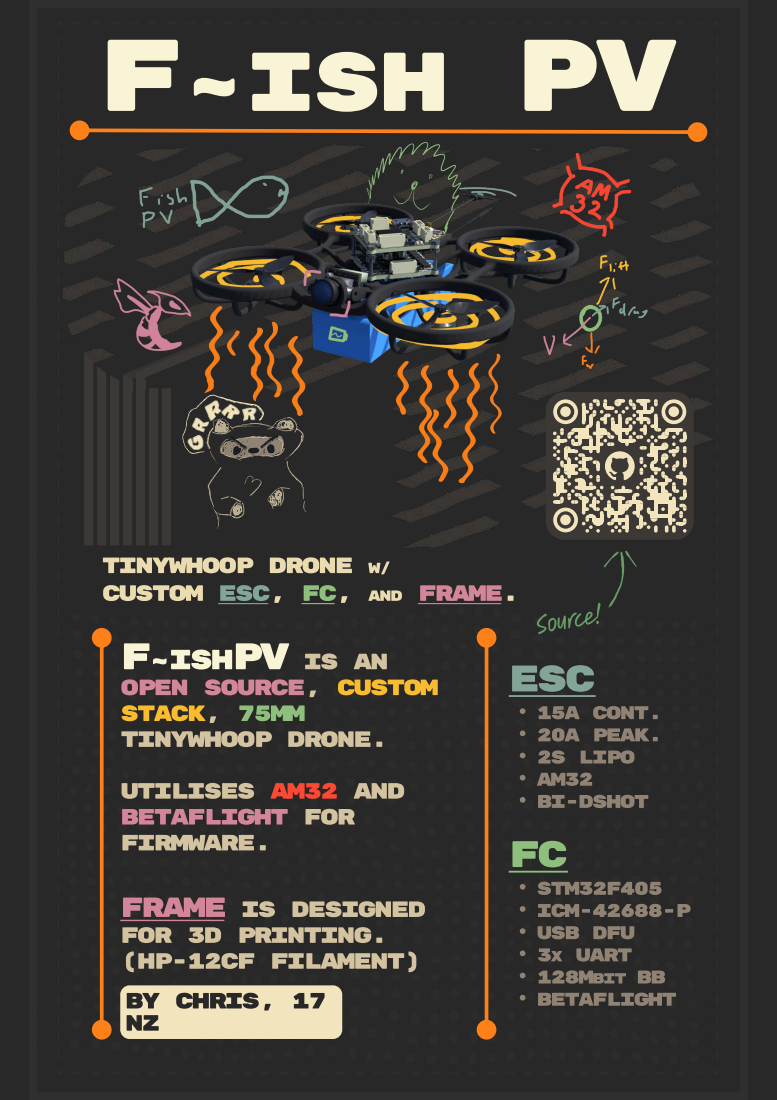
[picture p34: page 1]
Tinywhoop drone w/; custom ESC, FC, and; frame. Source!; utilises AM32 and Betaflight for; FIRMWARE.; By Chris, 17 Nz; ESC; 15A Cont. 20A Peak. 2S LIPO; BI⁻DSHOT; STM32F405 ICM⁻42688⁻P; USB DFU; 3x UART 128MBIT BB Betaflight

F~ishPV is an

open source, custom
stack, 75mm
tinywhoop drone.

frame is designed
for 3d printing.
(HP⁻12CF filament)

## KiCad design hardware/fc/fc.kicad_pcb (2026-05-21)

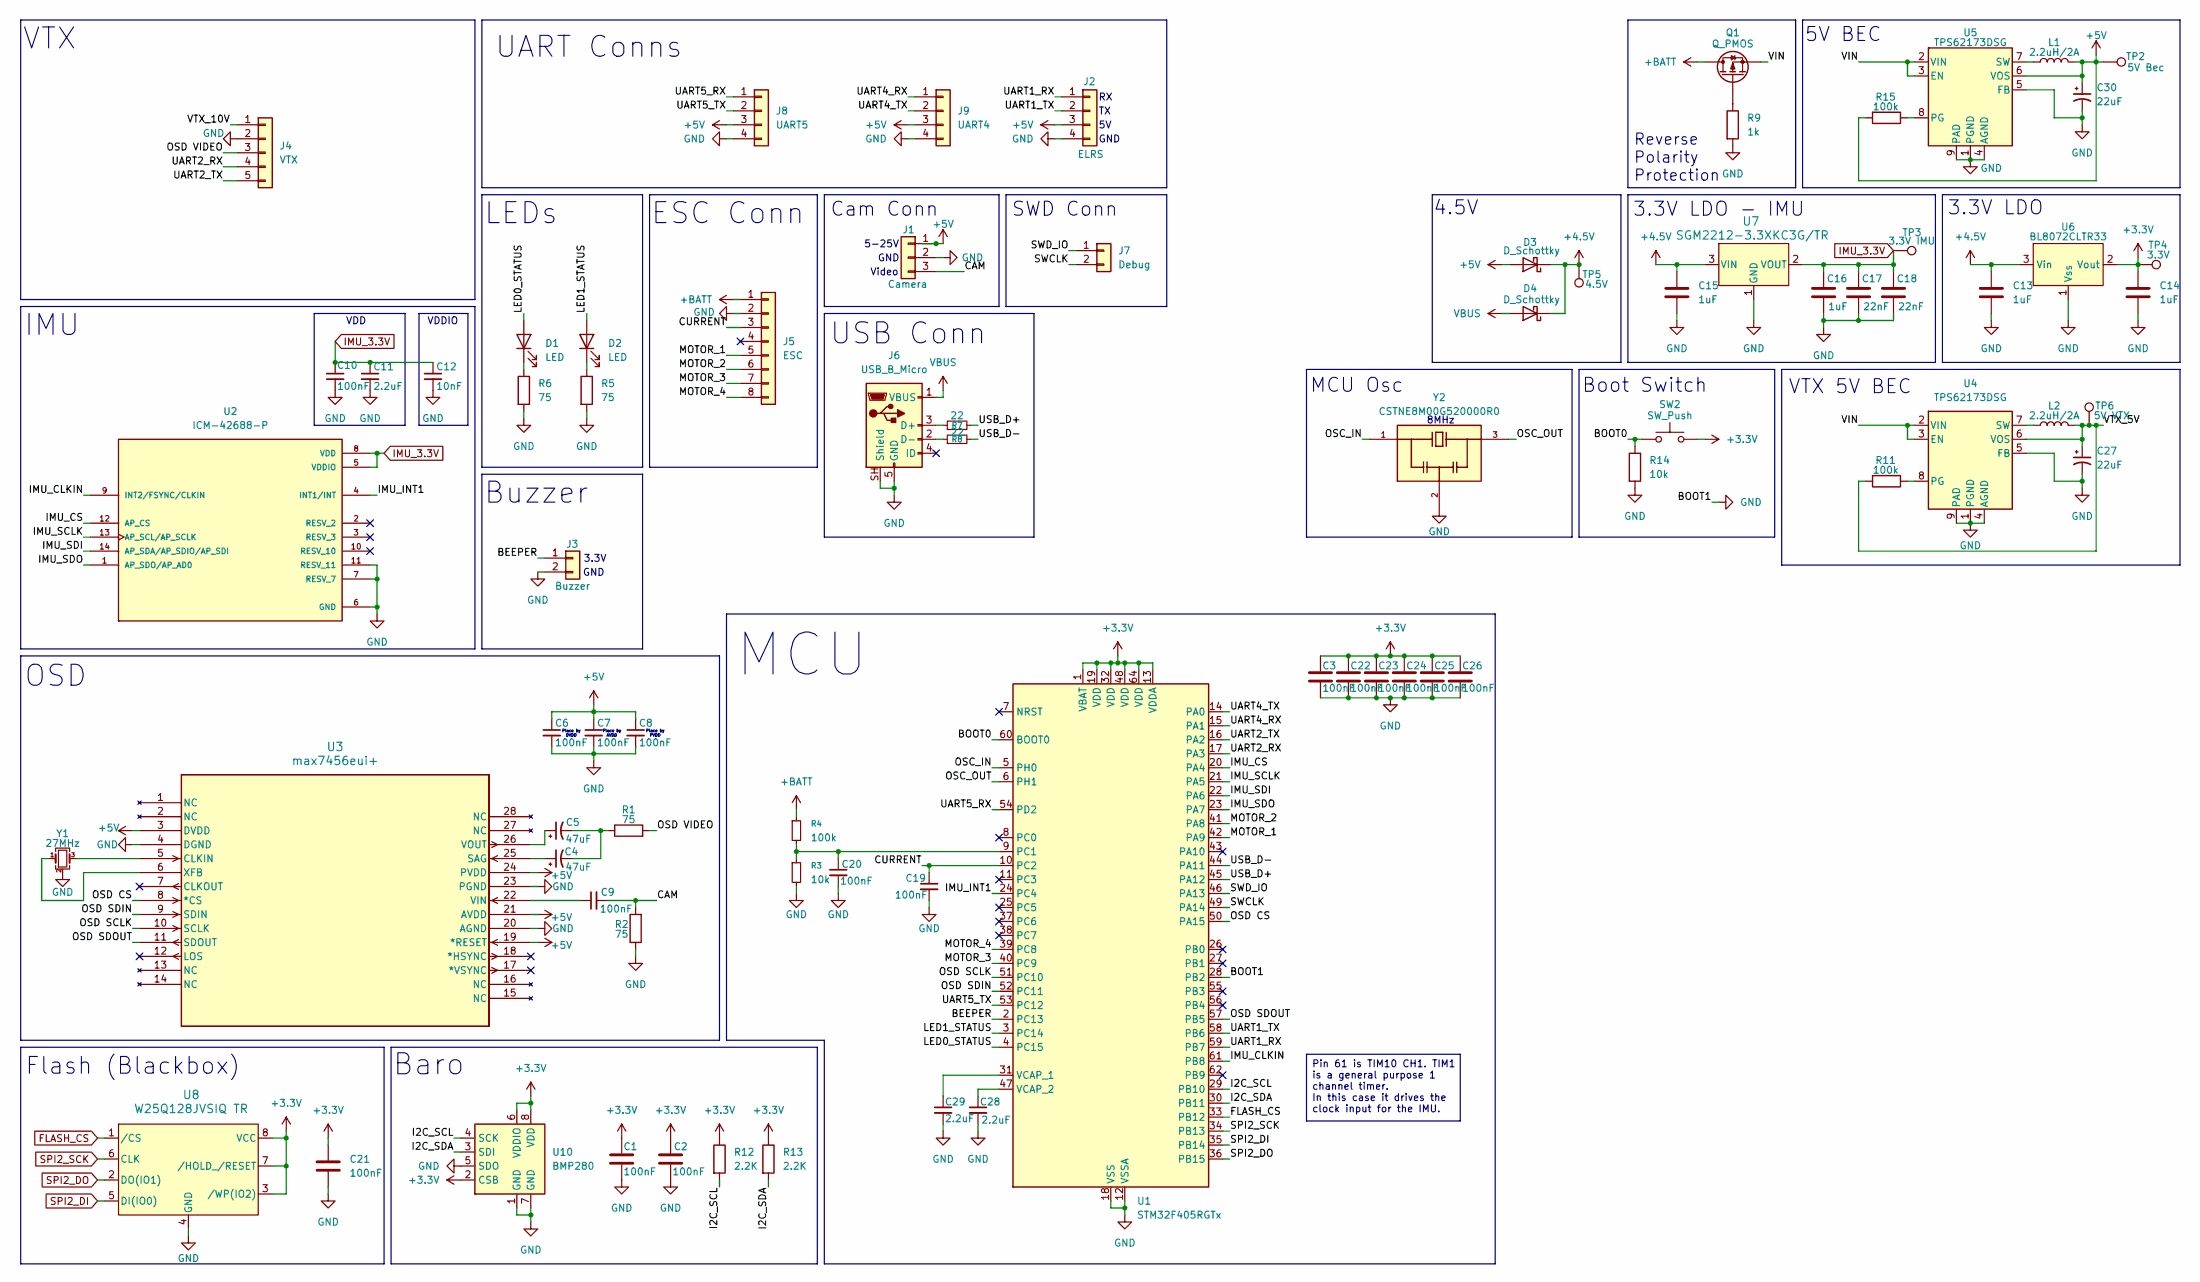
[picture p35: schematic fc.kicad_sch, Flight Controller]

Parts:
C1, C2, C3, C6, C7, C8, C9, C10, C19, C20, C21, C22, C23, C24, C25, C26: 100nF; C_0402_1005Metric
C4, C5: 47uF; CP_Elec_4x5.4
C11, C28, C29: 2.2uF; C_0402_1005Metric
C12: 10nF; C_0402_1005Metric
C13, C14, C15, C16: 1uF; C_0402_1005Metric
C17, C18: 22nF; C_0402_1005Metric
C27, C30: 22uF; CP_Elec_4x5.4
D1, D2: LED; LED_0603_1608Metric
D3, D4: D_Schottky; D_SOD-323
J1: Camera; JST_SH_BM03B-SRSS-TB_1x03-1MP_P1.00mm_Vertical
J2: ELRS; JST_SH_BM04B-SRSS-TB_1x04-1MP_P1.00mm_Vertical
J3: Buzzer; SolderWire-0.1sqmm_1x02_P3.6mm_D0.4mm_OD1mm
J4: VTX; JST_SH_BM05B-SRSS-TB_1x05-1MP_P1.00mm_Vertical
J5: ESC; JST_SH_BM08B-SRSS-TB_1x08-1MP_P1.00mm_Vertical
J6: USB_B_Micro; SHOUHAN_MICROXNJ
J7: Debug; SolderWire-0.1sqmm_1x02_P3.6mm_D0.4mm_OD1mm
J8: UART5; JST_SH_BM04B-SRSS-TB_1x04-1MP_P1.00mm_Vertical
J9: UART4; JST_SH_BM04B-SRSS-TB_1x04-1MP_P1.00mm_Vertical
L1, L2: 2.2uH/2A; INDC1608X95N
Q1: Q_PMOS; SOT-23
R1, R2, R5, R6: 75; R_0402_1005Metric
R3, R14: 10k; R_0402_1005Metric
R4, R11, R15: 100k; R_0402_1005Metric
R7, R8: 22; R_0402_1005Metric
R9: 1k; R_0402_1005Metric
R12, R13: 2.2K; R_0402_1005Metric
SW2: SW_Push; SW_TS-1088-AR02016
TP2: 5V Bec; TestPoint_Pad_D1.0mm
TP3: 3.3V IMU; TestPoint_Pad_D1.0mm
TP4: 3.3V; TestPoint_Pad_D1.0mm
TP5: 4.5V; TestPoint_Pad_D1.0mm
TP6: 5V VTX; TestPoint_Pad_D1.0mm
U1: STM32F405RGTx; LQFP-64_10x10mm_P0.5mm
U2: ICM-42688-P; PQFN50P300X250X97-14N; PARTREV 1.2
U3: max7456eui+; 21-0108G_U28E-5_MXM
U4, U5: TPS62173DSG; WSON-8-1EP_2x2mm_P0.5mm_EP0.9x1.6mm_ThermalVias
U6: BL8072CLTR33; SOT-223-3_TabPin2
U7: SGM2212-3.3XKC3G/TR; SOT-223-3_TabPin2
U8: W25Q128JVSIQ TR; SOIC_208MIL_WIN
U10: BMP280; Bosch_LGA-8_2x2.5mm_P0.65mm_ClockwisePinNumbering
Y1: 27MHz; Crystal_SMD_3225-4Pin_3.2x2.5mm
Y2: CSTNE8M00G520000R0; OSC_CSTNE8M00G520000R0; PARTREV JGC42-8858A

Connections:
+3.3V: C1.1, C2.1, C3.1, C14.1, C21.1, C22.1, C23.1, C24.1, C25.1, C26.1, R12.1, R13.1, SW2.2, TP4.1, U1.1 (VBAT), U1.13 (VDDA), U1.19 (VDD), U1.32 (VDD), U1.48 (VDD), U1.64 (VDD), U6.2 (Vout), U8.3 (/WP(IO2)), U8.7 (/HOLD_/RESET), U8.8 (VCC), U10.2 (CSB), U10.6 (VDDIO), U10.8 (VDD); also elsewhere on the board
+4.5V: C13.1, C15.1, D3.1 (K), D4.1 (K), TP5.1 (1_1), U6.3 (Vin), U7.3 (VIN)
+5V: C6.1, C7.1, C8.1, C30.1, D3.2 (A), J1.1, J2.3, J8.3, J9.3, L1.2, R15.2, TP2.1, U3.3 (DVDD), U3.19 (*RESET), U3.21 (AVDD), U3.24 (PVDD), U5.6 (VOS); also elsewhere on the board
+BATT: J5.1, Q1.D, R4.1
/BEEPER: J3.1, U1.2 (PC13)
/BOOT0: R14.1, SW2.1, U1.60 (BOOT0)
/CAM: C9.2, J1.3, R2.2
/CURRENT: C19.1, J5.3, U1.10 (PC2)
/I2C_SCL: R12.2, U1.29 (PB10), U10.4 (SCK)
/I2C_SDA: R13.2, U1.30 (PB11), U10.3 (SDI)
/IMU_CLKIN: U1.61 (PB8), U2.9 (INT2/FSYNC/CLKIN)
/IMU_CS: U1.20 (PA4), U2.12 (AP_CS)
/IMU_INT1: U1.24 (PC4), U2.4 (INT1/INT)
/IMU_SCLK: U1.21 (PA5), U2.13 (AP_SCL/AP_SCLK)
/IMU_SDI: U1.22 (PA6), U2.14 (AP_SDA/AP_SDIO/AP_SDI)
/IMU_SDO: U1.23 (PA7), U2.1 (AP_SDO/AP_AD0)
/LED0_STATUS: D1.2 (A), U1.4 (PC15)
/LED1_STATUS: D2.2 (A), U1.3 (PC14)
/MOTOR_1: J5.5, U1.42 (PA9)
/MOTOR_2: J5.6, U1.41 (PA8)
/MOTOR_3: J5.7, U1.40 (PC9)
/MOTOR_4: J5.8, U1.39 (PC8)
/OSC_IN: U1.5 (PH0), Y2.1
/OSC_OUT: U1.6 (PH1), Y2.3
/OSD CS: U1.50 (PA15), U3.8 (*CS)
/OSD SCLK: U1.51 (PC10), U3.10 (SCLK)
/OSD SDIN: U1.52 (PC11), U3.9 (SDIN)
/OSD SDOUT: U1.57 (PB5), U3.11 (SDOUT)
/OSD VIDEO: J4.3, R1.2
/SWCLK: J7.2, U1.49 (PA14)
/SWD_IO: J7.1, U1.46 (PA13)
/UART1_RX: J2.1, U1.59 (PB7)
/UART1_TX: J2.2, U1.58 (PB6)
/UART2_RX: J4.4, U1.17 (PA3)
/UART2_TX: J4.5, U1.16 (PA2)
/UART4_RX: J9.1, U1.15 (PA1)
/UART4_TX: J9.2, U1.14 (PA0)
/UART5_RX: J8.1, U1.54 (PD2)
/UART5_TX: J8.2, U1.53 (PC12)
/USB_D+: R7.2, U1.45 (PA12)
/USB_D-: R8.2, U1.44 (PA11)
/VIN: Q1.S, U4.2 (VIN), U4.3 (EN), U5.2 (VIN), U5.3 (EN)
/VTX_5V: C27.1, L2.2, R11.2, TP6.1, U4.6 (VOS); also elsewhere on the board
/VTX_10V: J4.1
FLASH_CS: U1.33 (PB12), U8.1 (/CS)
GND: C1.2, C2.2, C3.2, C6.2, C7.2, C8.2, C10.2, C11.2, C12.2, C13.2, C14.2, C15.2, C16.2, C17.2, C18.2, C19.2, C20.2, C21.2, C22.2, C23.2, C24.2, C25.2, C26.2, C27.2, C28.2, C29.2, C30.2, J1.2, J2.4, J3.2, J4.2, J5.2, J6.5 (GND), J6.S3, J6.S4, J6.S5, J6.S6, J6.SH (Shield), J8.4, J9.4, R2.1, R3.2, R5.2, R6.2, R9.2, R14.2, U1.12 (VSSA), U1.18 (VSS), U1.28 (PB2), U1.63 (VSS), U2.6 (GND), U2.7 (RESV_7), U2.11 (RESV_11), U3.4 (DGND), U3.20 (AGND), U3.23 (PGND), U4.1 (PGND), U4.4 (AGND), U4.5 (FB), U4.9 (PAD), U5.1 (PGND), U5.4 (AGND), U5.5 (FB), U5.9 (PAD), U6.1 (Vss), U7.1 (GND), U8.4 (GND), U10.1 (GND), U10.5 (SDO), U10.7 (GND), Y1.2 (G), Y1.4 (G), Y2.2
IMU_3.3V: C10.1, C11.1, C12.1, C16.1, C17.1, C18.1, TP3.1, U2.5 (VDDIO), U2.8 (VDD), U7.2 (VOUT); also elsewhere on the board
unnamed: C4.2, C5.2, R1.1
unnamed: D1.1 (K), R6.1
unnamed: D2.1 (K), R5.1
unnamed: J6.3 (D+), R7.1
unnamed: J6.2 (D-), R8.1
unnamed: Q1.G, R9.1
unnamed: C20.1, R3.1, R4.2, U1.9 (PC1)
unnamed: C29.1, U1.31 (VCAP_1)
unnamed: C28.1, U1.47 (VCAP_2)
unnamed: U3.5 (CLKIN), Y1.3
unnamed: C4.1, U3.25 (SAG)
unnamed: C9.1, U3.22 (VIN)
unnamed: C5.1, U3.26 (VOUT)
unnamed: U3.6 (XFB), Y1.1
unnamed: R11.1, U4.8 (PG)
unnamed: L2.1, U4.7 (SW)
unnamed: R15.1, U5.8 (PG)
unnamed: L1.1, U5.7 (SW)
SPI2_DI: U1.35 (PB14), U8.5 (DI(IO0))
SPI2_DO: U1.36 (PB15), U8.2 (DO(IO1))
SPI2_SCK: U1.34 (PB13), U8.6 (CLK)
VBUS: D4.2 (A), J6.1 (VBUS)

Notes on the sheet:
ESC Conn
GND
8MHz
Reverse Polarity Protection
VDD
VTX
Place by DVDD
5-25V
USB Conn
Flash (Blackbox)
Place by AVDD
Cam Conn
Baro
3.3V LDO - IMU
SWD Conn
OSD
Boot Switch
UART Conns
VTX 5V BEC
3.3V
5V BEC
Buzzer
IMU
4.5V
MCU
GND
VDDIO
MCU Osc
LEDs
3.3V LDO
Video
Place by PVDD
Pin 61 is TIM10 CH1. TIM1 is a general purpose 1 channel timer. In this case it drives the clock input for the IMU.

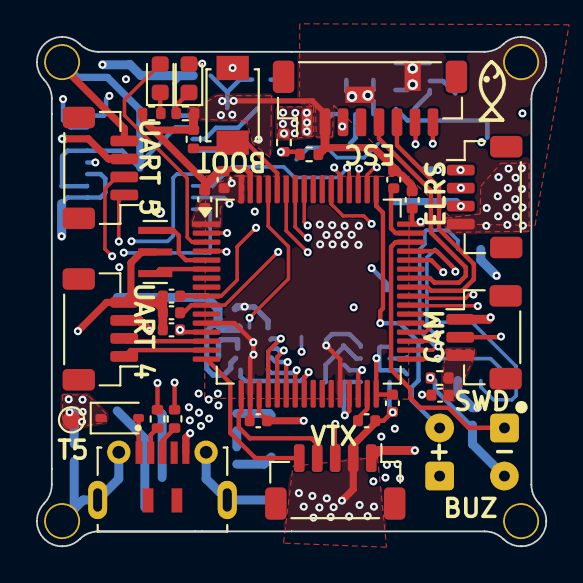
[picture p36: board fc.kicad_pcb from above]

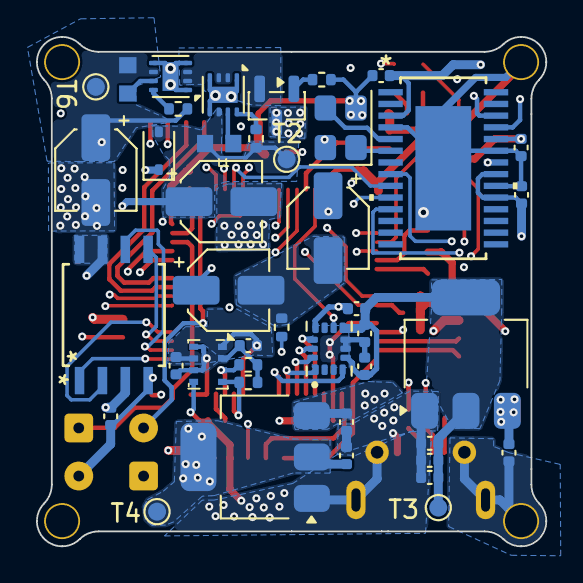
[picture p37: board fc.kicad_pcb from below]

Board: 6 copper layers, 28.3 x 28.3 mm, 77 parts (42 on the bottom side), 68 nets.

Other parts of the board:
T2: 5V Bec; TestPoint_Pad_D1.0mm
T3: 3.3V IMU; TestPoint_Pad_D1.0mm
T4: 3.3V; TestPoint_Pad_D1.0mm
T6: 5V VTX; TestPoint_Pad_D1.0mm

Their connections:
+3.3V: T4.1 (1_1); also elsewhere on the board
+5V: T2.1 (1_1); also elsewhere on the board
/VTX_5V: T6.1 (1_1); also elsewhere on the board
IMU_3.3V: T3.1 (1_1); also elsewhere on the board

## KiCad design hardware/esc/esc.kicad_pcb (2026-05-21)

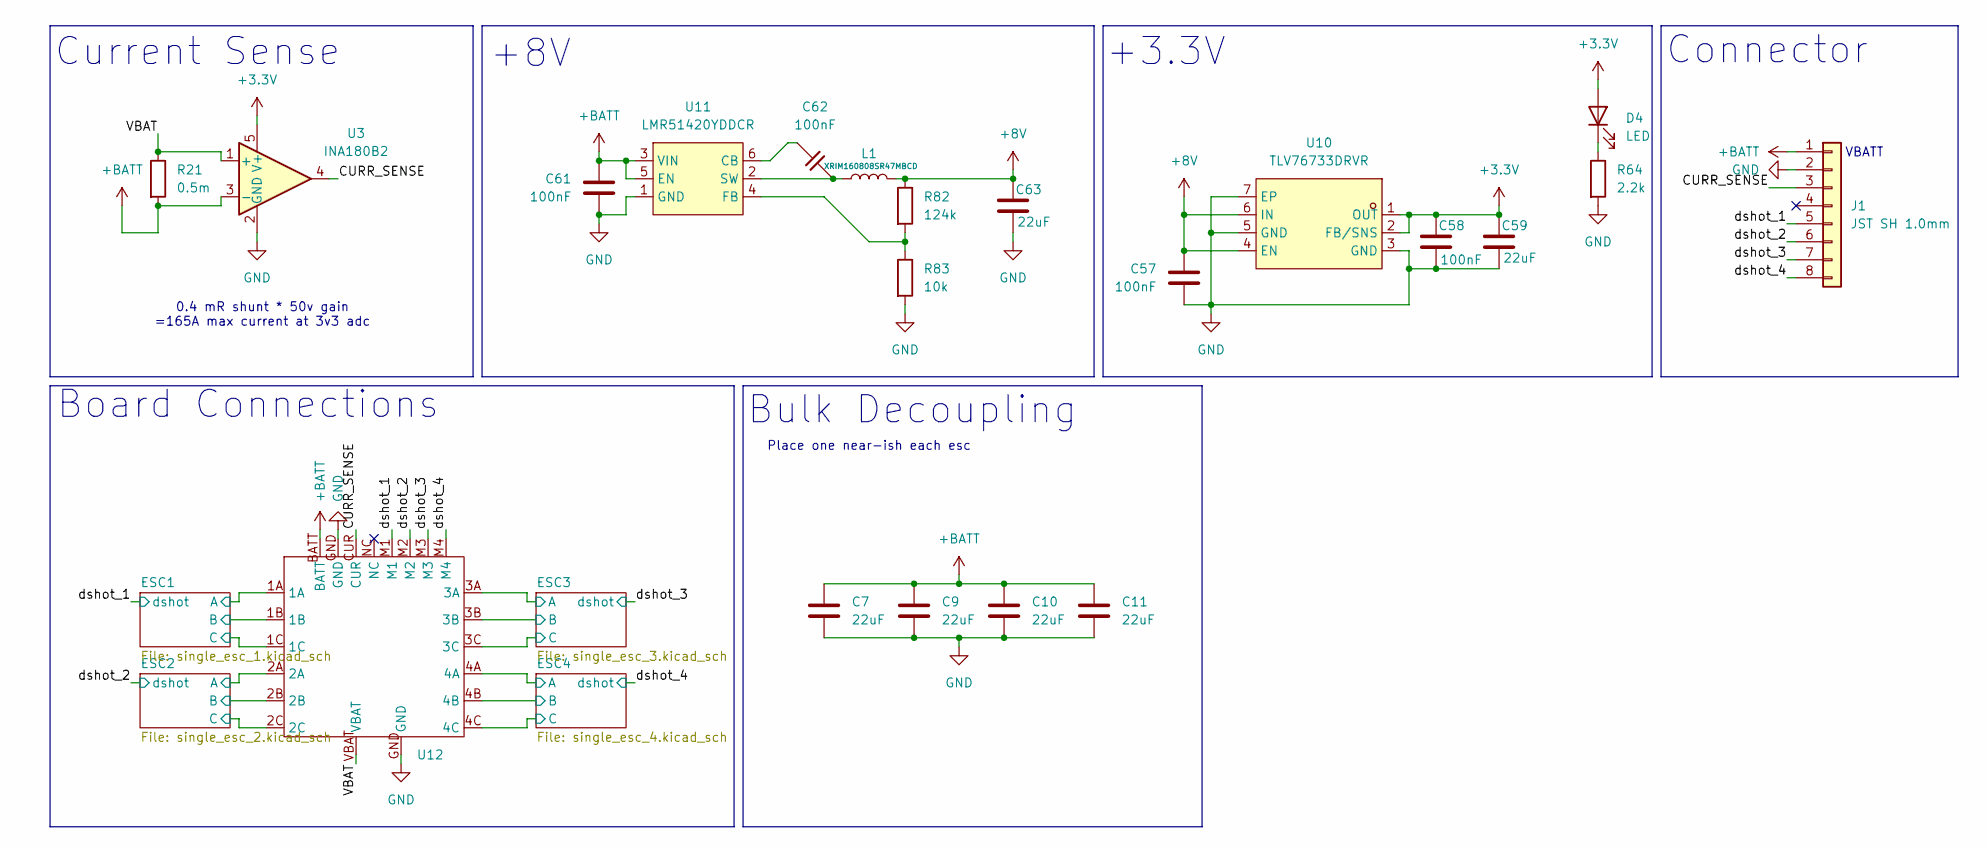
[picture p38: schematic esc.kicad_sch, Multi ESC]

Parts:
C7, C9, C10, C11: 22uF; C_0603_1608Metric
C57, C58, C61, C62: 100nF; C_0402_1005Metric
C59, C63: 22uF; C_0805_2012Metric
D4: LED; LED_0603_1608Metric
J1: JST SH 1.0mm; JST_SM08B-SRSS-TB_LF__SN_
L1: XRIM160808SR47MBCD; L_0603_1608Metric
R21: 0.5m; BVNZR000510
R64: 2.2k; R_0402_1005Metric
R82: 124k; R_0603_1608Metric
R83: 10k; R_0402_1005Metric
U3: INA180B2; SOT-23-5
U10: TLV76733DRVR; WSON-6_L2.0-W2.0-P0.65-TL-EP; LCSC Part C2848334
U11: LMR51420YDDCR; SOT-23-6_L2.9-W1.6-P0.95-LS2.9-BL; LCSC Part C5383002
U12: BoardPlate

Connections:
+3.3V: C58.2, C59.2, D4.2 (A), U3.5 (V+), U10.1 (OUT), U10.2 (FB/SNS); also elsewhere on the board
+8V: C57.1, C63.2, L1.2, R82.1, U10.4 (EN), U10.6 (IN); also elsewhere on the board
+BATT: C7.1, C9.1, C10.1, C11.1, C61.1, J1.1, R21.2, U3.3 (-), U11.3 (VIN), U11.5 (EN), U12.BATT; also elsewhere on the board
/CURR_SENSE: J1.3, U3.4, U12.CUR
/ESC1/FloatA: U12.1A; also elsewhere on the board
/ESC1/FloatB: U12.1B; also elsewhere on the board
/ESC1/FloatC: U12.1C; also elsewhere on the board
/ESC2/FloatA: U12.2A; also elsewhere on the board
/ESC2/FloatB: U12.2B; also elsewhere on the board
/ESC2/FloatC: U12.2C; also elsewhere on the board
/ESC3/FloatA: U12.3A; also elsewhere on the board
/ESC3/FloatB: U12.3B; also elsewhere on the board
/ESC3/FloatC: U12.3C; also elsewhere on the board
/ESC4/FloatA: U12.4A; also elsewhere on the board
/ESC4/FloatB: U12.4B; also elsewhere on the board
/ESC4/FloatC: U12.4C; also elsewhere on the board
/VBAT: R21.1, U3.1 (+), U12.VBAT
/dshot_1: J1.5, U12.M1; also elsewhere on the board
/dshot_2: J1.6, U12.M2; also elsewhere on the board
/dshot_3: J1.7, U12.M3; also elsewhere on the board
/dshot_4: J1.8, U12.M4; also elsewhere on the board
GND: C7.2, C9.2, C10.2, C11.2, C57.2, C58.1, C59.1, C61.2, C63.1, J1.2, R64.2, R83.2, U3.2 (GND), U10.3 (GND), U10.5 (GND), U10.7 (EP), U11.1 (GND), U12.GND; also elsewhere on the board
unnamed: D4.1 (K), R64.1
unnamed: C62.2, U11.6 (CB)
unnamed: R82.2, R83.1, U11.4 (FB)
unnamed: C62.1, L1.1, U11.2 (SW)

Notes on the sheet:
+8V
0.4 mR shunt * 50v gain =165A max current at 3v3 adc
Connector
Current Sense
VBATT
Bulk Decoupling
+3.3V
Place one near-ish each esc
Board Connections

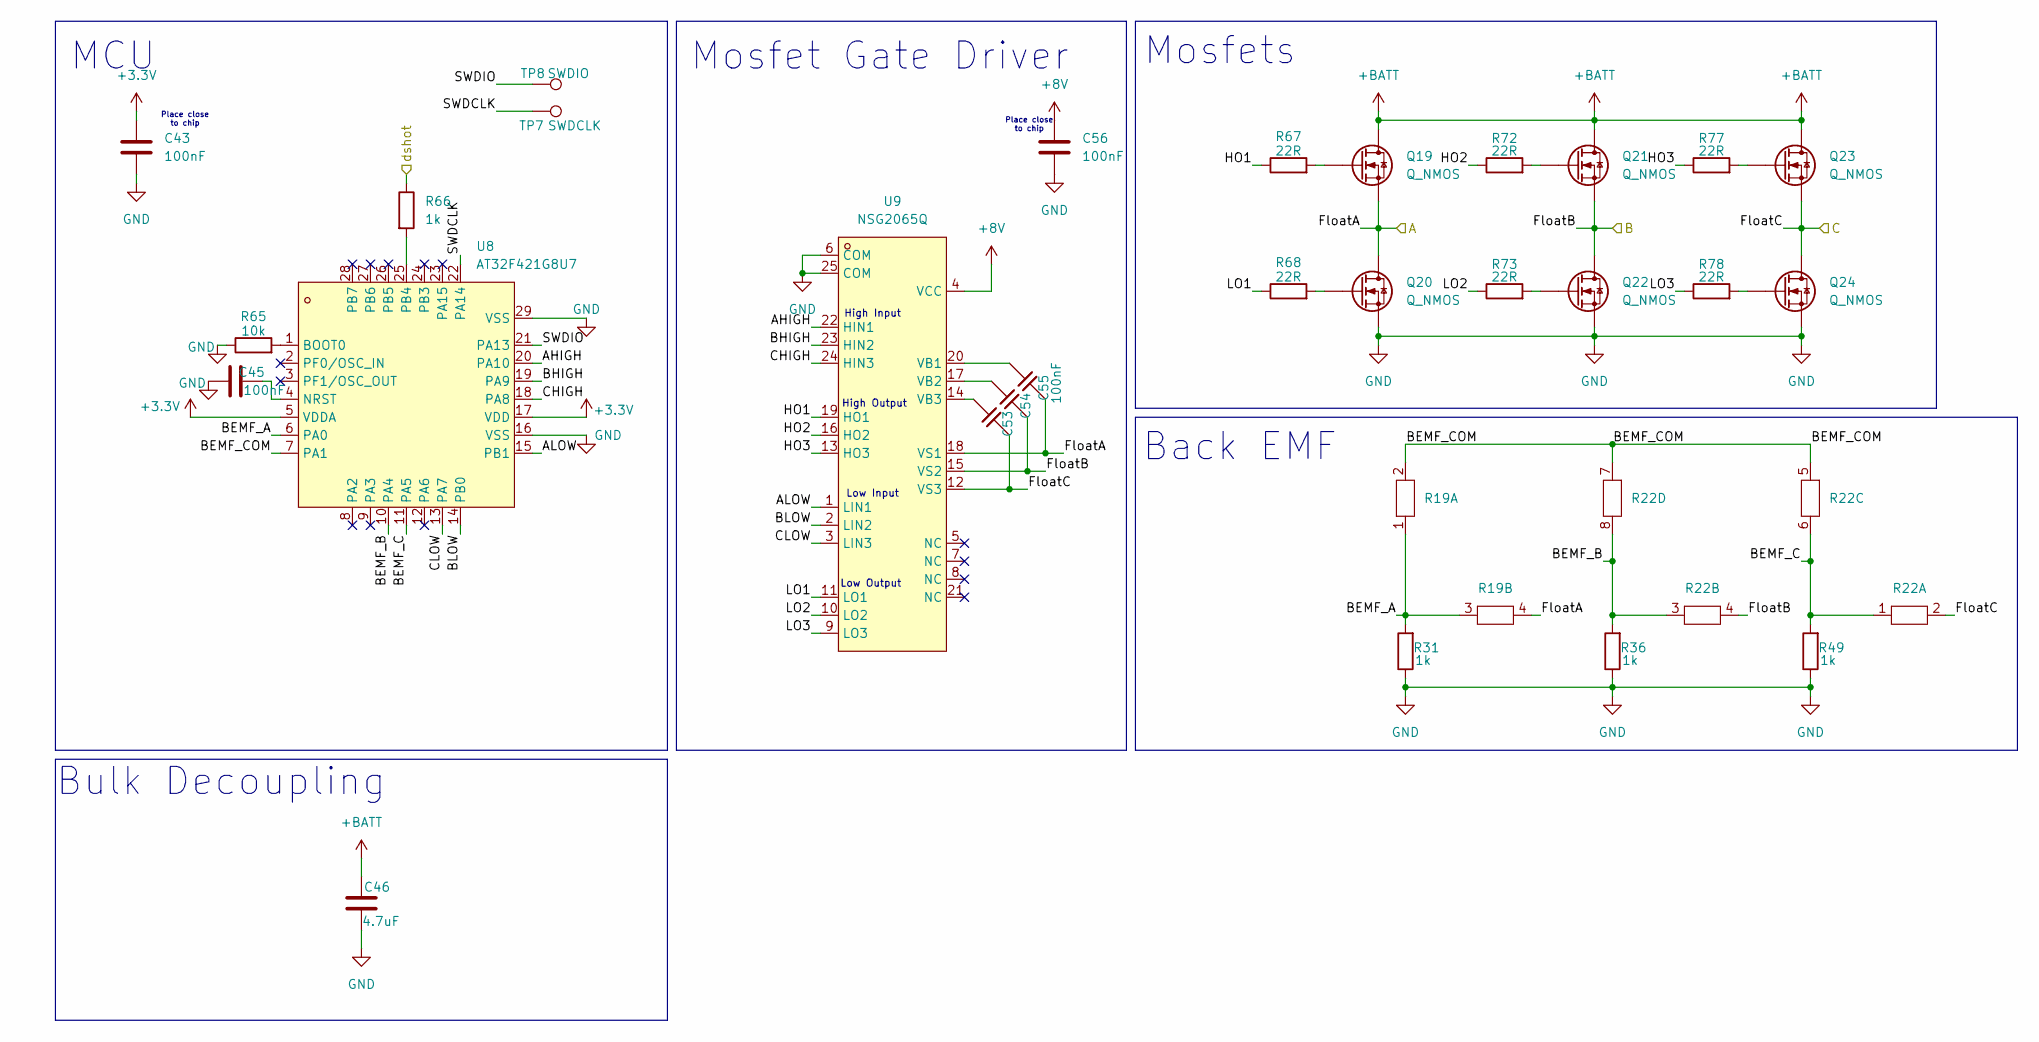
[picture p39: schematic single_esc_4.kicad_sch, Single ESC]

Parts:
C43, C45, C53, C54, C55, C56: 100nF; C_0402_1005Metric
C46: 4.7uF; C_0603_1608Metric
Q19, Q20, Q21, Q22, Q23, Q24: Q_NMOS; POWERPAK-1212-8_L3.0-W3.0-P0.65-LS3.3-BL
R19, R22: RES_4D03_0603_3P2X1P6_ROH
R31, R36, R49, R66: 1k; R_0402_1005Metric
R65: 10k; R_0402_1005Metric
R67, R68, R72, R73, R77, R78: 22R; R_0402_1005Metric
TP7: SWDCLK; TestPoint_Pad_D1.0mm
TP8: SWDIO; TestPoint_Pad_D1.0mm
U8: AT32F421G8U7; QFN-28_L4.0-W4.0-P0.40-TL-EP2.4; LCSC Part C2765098
U9: NSG2065Q; QFN-24_L4.0-W4.0-P0.50-TL-EP2.8; LCSC Part C41414478

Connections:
+3.3V: C43.1, U8.5 (VDDA), U8.17 (VDD); also elsewhere on the board
+8V: C56.1, U9.4 (VCC); also elsewhere on the board
+BATT: C46.1, Q19.D, Q21.D, Q23.D; also elsewhere on the board
/ESC4/AHIGH: U8.20 (PA10), U9.22 (HIN1)
/ESC4/ALOW: U8.15 (PB1), U9.1 (LIN1)
/ESC4/BEMF_A: R19.1, R19.3, R31.2, U8.6 (PA0)
/ESC4/BEMF_B: R22.3, R22.8, R36.2, U8.10 (PA4)
/ESC4/BEMF_C: R22.1, R22.6, R49.2, U8.11 (PA5)
/ESC4/BEMF_COM: R19.2, R22.5, R22.7, U8.7 (PA1)
/ESC4/BHIGH: U8.19 (PA9), U9.23 (HIN2)
/ESC4/BLOW: U8.14 (PB0), U9.2 (LIN2)
/ESC4/CHIGH: U8.18 (PA8), U9.24 (HIN3)
/ESC4/CLOW: U8.13 (PA7), U9.3 (LIN3)
/ESC4/FloatA: C55.1, Q19.S, Q20.D, R19.4, U9.18 (VS1); also elsewhere on the board
/ESC4/FloatB: C54.1, Q21.S, Q22.D, R22.4, U9.15 (VS2); also elsewhere on the board
/ESC4/FloatC: C53.1, Q23.S, Q24.D, R22.2, U9.12 (VS3); also elsewhere on the board
/ESC4/HO1: R67.1, U9.19 (HO1)
/ESC4/HO2: R72.1, U9.16 (HO2)
/ESC4/HO3: R77.1, U9.13 (HO3)
/ESC4/LO1: R68.1, U9.11 (LO1)
/ESC4/LO2: R73.1, U9.10 (LO2)
/ESC4/LO3: R78.1, U9.9 (LO3)
/ESC4/SWDCLK: TP7.1, U8.22 (PA14); also elsewhere on the board
/ESC4/SWDIO: TP8.1, U8.21 (PA13); also elsewhere on the board
/dshot_4: R66.1; also elsewhere on the board
GND: C43.2, C45.2, C46.2, C56.2, Q20.S, Q22.S, Q24.S, R31.1, R36.1, R49.1, R65.1, U8.16 (VSS), U8.29 (VSS), U9.6 (COM), U9.25 (COM); also elsewhere on the board
unnamed: Q19.G, R67.2
unnamed: Q20.G, R68.2
unnamed: Q21.G, R72.2
unnamed: Q22.G, R73.2
unnamed: Q23.G, R77.2
unnamed: Q24.G, R78.2
unnamed: R65.2, U8.1 (BOOT0)
unnamed: C45.1, U8.4 (NRST)
unnamed: R66.2, U8.25 (PB4)
unnamed: C55.2, U9.20 (VB1)
unnamed: C54.2, U9.17 (VB2)
unnamed: C53.2, U9.14 (VB3)

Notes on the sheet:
High Output
Bulk Decoupling
MCU
High Input
Back EMF
Place close to chip
Mosfets
Low Output
Mosfet Gate Driver
Low Input

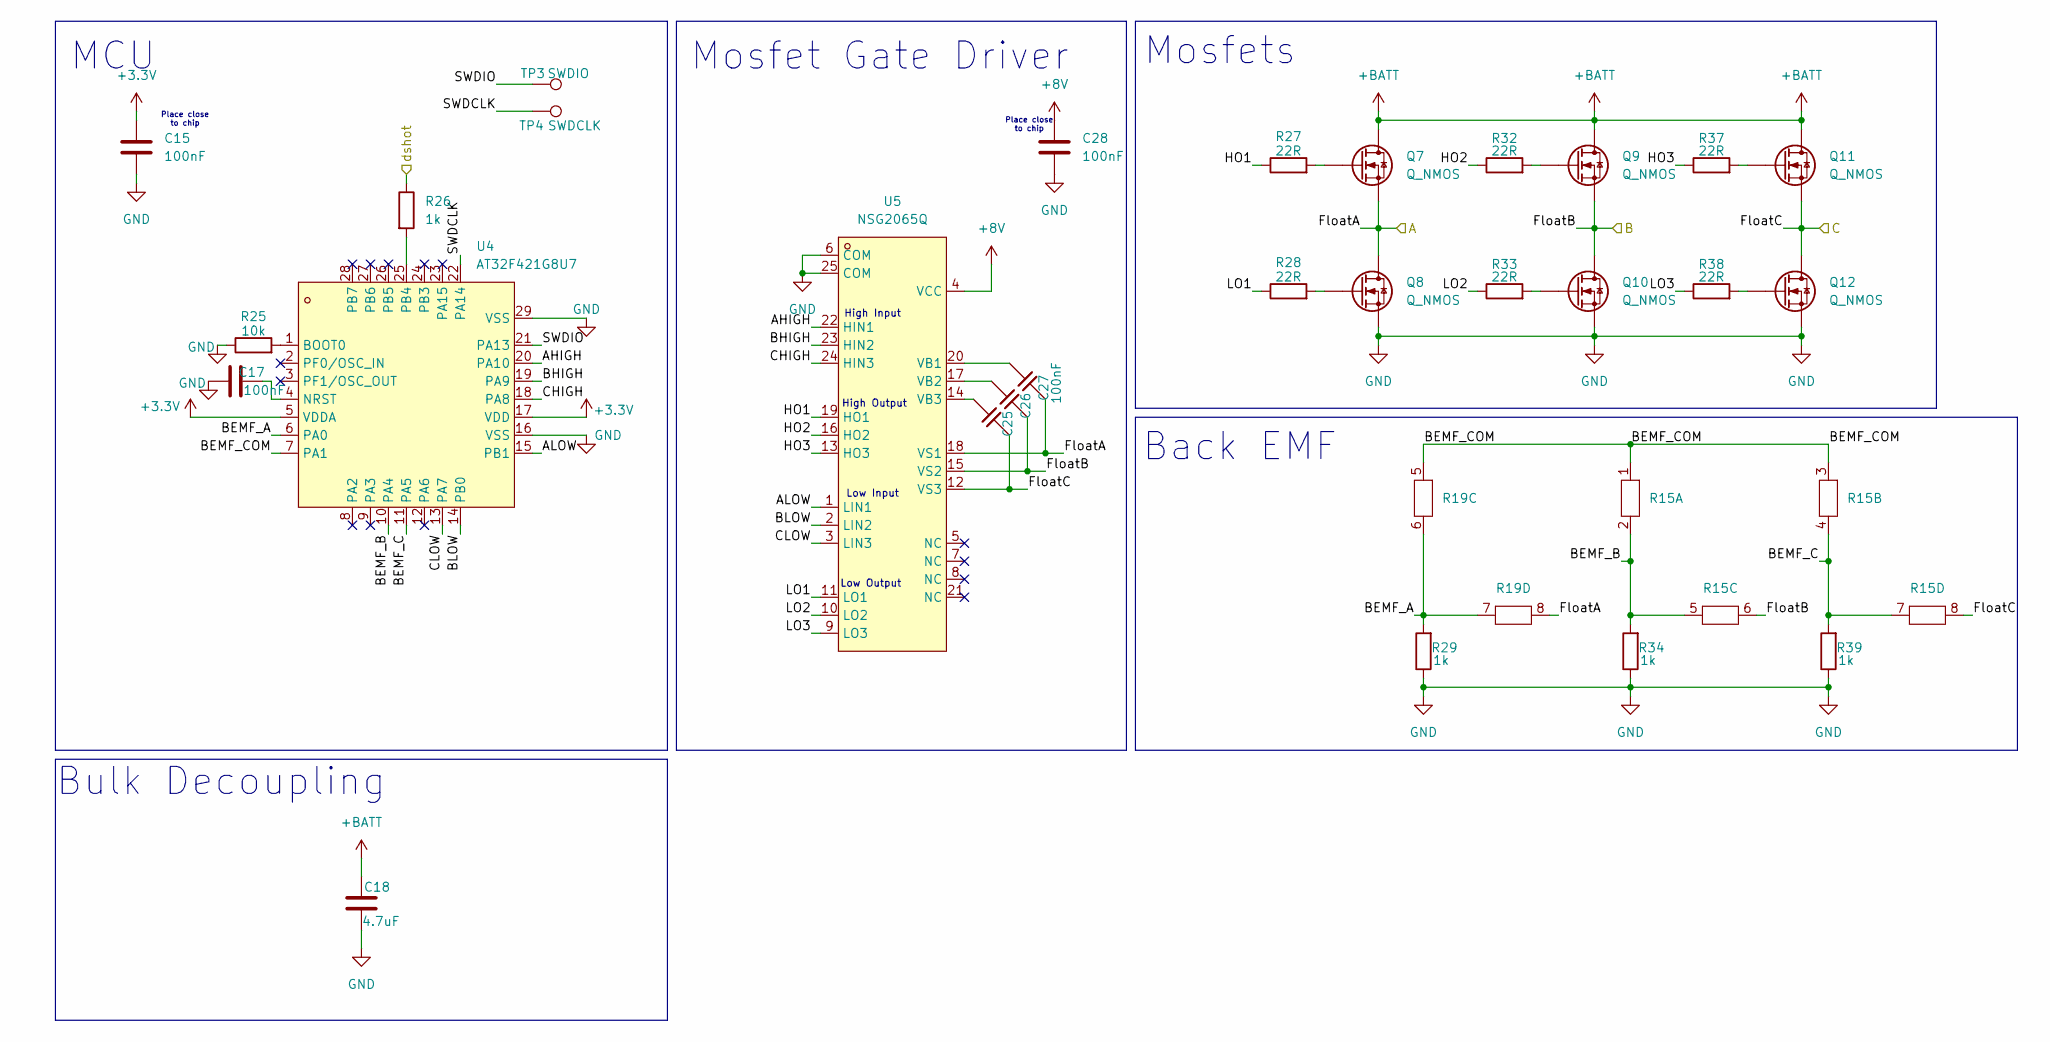
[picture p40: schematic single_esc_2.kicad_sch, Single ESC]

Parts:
C15, C17, C25, C26, C27, C28: 100nF; C_0402_1005Metric
C18: 4.7uF; C_0603_1608Metric
Q7, Q8, Q9, Q10, Q11, Q12: Q_NMOS; POWERPAK-1212-8_L3.0-W3.0-P0.65-LS3.3-BL
R15, R19: RES_4D03_0603_3P2X1P6_ROH
R25: 10k; R_0402_1005Metric
R26, R29, R34, R39: 1k; R_0402_1005Metric
R27, R28, R32, R33, R37, R38: 22R; R_0402_1005Metric
TP3: SWDIO; TestPoint_Pad_D1.0mm
TP4: SWDCLK; TestPoint_Pad_D1.0mm
U4: AT32F421G8U7; QFN-28_L4.0-W4.0-P0.40-TL-EP2.4; LCSC Part C2765098
U5: NSG2065Q; QFN-24_L4.0-W4.0-P0.50-TL-EP2.8; LCSC Part C41414478

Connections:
+3.3V: C15.1, U4.5 (VDDA), U4.17 (VDD); also elsewhere on the board
+8V: C28.1, U5.4 (VCC); also elsewhere on the board
+BATT: C18.1, Q7.D, Q9.D, Q11.D; also elsewhere on the board
/ESC2/AHIGH: U4.20 (PA10), U5.22 (HIN1)
/ESC2/ALOW: U4.15 (PB1), U5.1 (LIN1)
/ESC2/BEMF_A: R19.6, R19.7, R29.2, U4.6 (PA0)
/ESC2/BEMF_B: R15.2, R15.5, R34.2, U4.10 (PA4)
/ESC2/BEMF_C: R15.4, R15.7, R39.2, U4.11 (PA5)
/ESC2/BEMF_COM: R15.1, R15.3, R19.5, U4.7 (PA1)
/ESC2/BHIGH: U4.19 (PA9), U5.23 (HIN2)
/ESC2/BLOW: U4.14 (PB0), U5.2 (LIN2)
/ESC2/CHIGH: U4.18 (PA8), U5.24 (HIN3)
/ESC2/CLOW: U4.13 (PA7), U5.3 (LIN3)
/ESC2/FloatA: C27.1, Q7.S, Q8.D, R19.8, U5.18 (VS1); also elsewhere on the board
/ESC2/FloatB: C26.1, Q9.S, Q10.D, R15.6, U5.15 (VS2); also elsewhere on the board
/ESC2/FloatC: C25.1, Q11.S, Q12.D, R15.8, U5.12 (VS3); also elsewhere on the board
/ESC2/HO1: R27.1, U5.19 (HO1)
/ESC2/HO2: R32.1, U5.16 (HO2)
/ESC2/HO3: R37.1, U5.13 (HO3)
/ESC2/LO1: R28.1, U5.11 (LO1)
/ESC2/LO2: R33.1, U5.10 (LO2)
/ESC2/LO3: R38.1, U5.9 (LO3)
/ESC2/SWDCLK: TP4.1, U4.22 (PA14); also elsewhere on the board
/ESC2/SWDIO: TP3.1, U4.21 (PA13); also elsewhere on the board
/dshot_2: R26.1; also elsewhere on the board
GND: C15.2, C17.2, C18.2, C28.2, Q8.S, Q10.S, Q12.S, R25.1, R29.1, R34.1, R39.1, U4.16 (VSS), U4.29 (VSS), U5.6 (COM), U5.25 (COM); also elsewhere on the board
unnamed: Q7.G, R27.2
unnamed: Q8.G, R28.2
unnamed: Q9.G, R32.2
unnamed: Q10.G, R33.2
unnamed: Q11.G, R37.2
unnamed: Q12.G, R38.2
unnamed: R25.2, U4.1 (BOOT0)
unnamed: C17.1, U4.4 (NRST)
unnamed: R26.2, U4.25 (PB4)
unnamed: C27.2, U5.20 (VB1)
unnamed: C26.2, U5.17 (VB2)
unnamed: C25.2, U5.14 (VB3)

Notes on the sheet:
MCU
High Output
Back EMF
High Input
Mosfet Gate Driver
Mosfets
Bulk Decoupling
Low Output
Place close to chip
Low Input

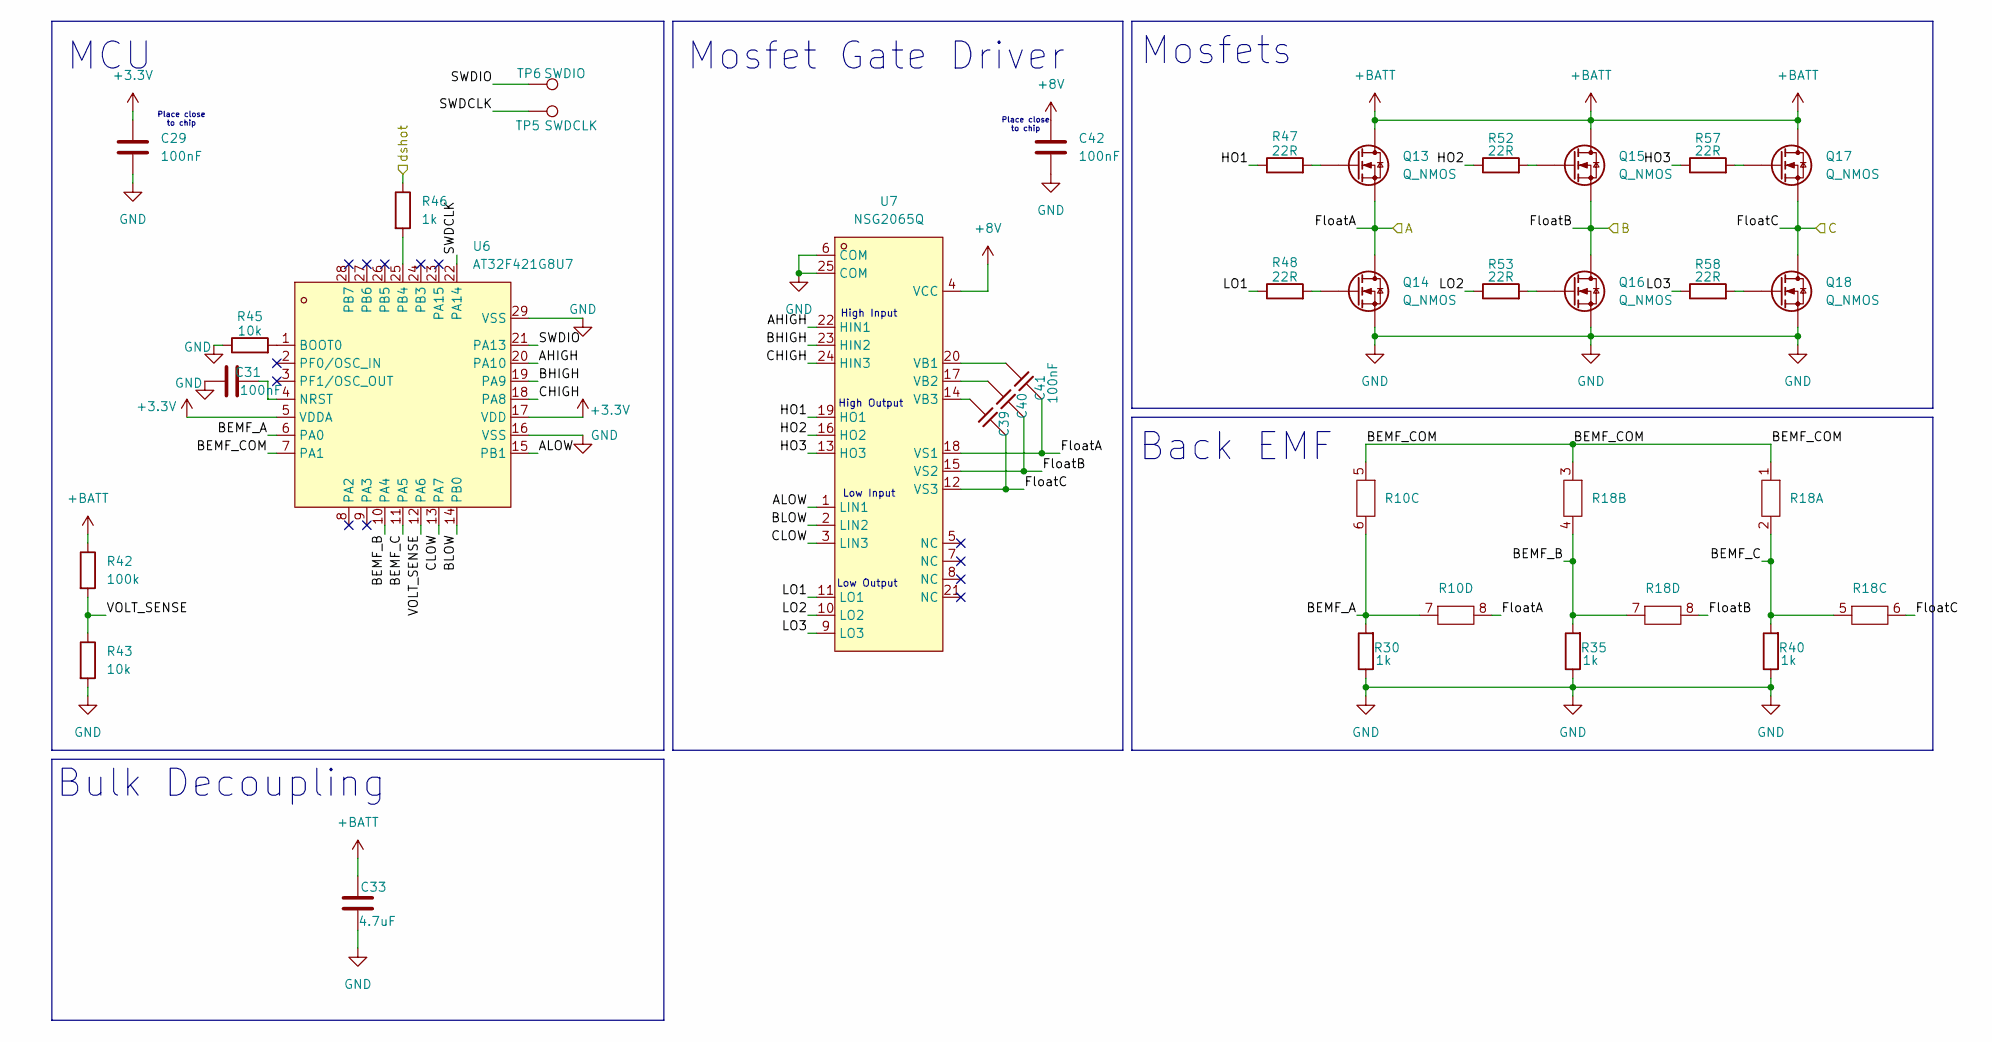
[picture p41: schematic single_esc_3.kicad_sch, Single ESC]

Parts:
C29, C31, C39, C40, C41, C42: 100nF; C_0402_1005Metric
C33: 4.7uF; C_0603_1608Metric
Q13, Q14, Q15, Q16, Q17, Q18: Q_NMOS; POWERPAK-1212-8_L3.0-W3.0-P0.65-LS3.3-BL
R10, R18: RES_4D03_0603_3P2X1P6_ROH
R30, R35, R40, R46: 1k; R_0402_1005Metric
R42: 100k; R_0402_1005Metric
R43, R45: 10k; R_0402_1005Metric
R47, R48, R52, R53, R57, R58: 22R; R_0402_1005Metric
TP5: SWDCLK; TestPoint_Pad_D1.0mm
TP6: SWDIO; TestPoint_Pad_D1.0mm
U6: AT32F421G8U7; QFN-28_L4.0-W4.0-P0.40-TL-EP2.4; LCSC Part C2765098
U7: NSG2065Q; QFN-24_L4.0-W4.0-P0.50-TL-EP2.8; LCSC Part C41414478

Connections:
+3.3V: C29.1, U6.5 (VDDA), U6.17 (VDD); also elsewhere on the board
+8V: C42.1, U7.4 (VCC); also elsewhere on the board
+BATT: C33.1, Q13.D, Q15.D, Q17.D, R42.1; also elsewhere on the board
/ESC3/AHIGH: U6.20 (PA10), U7.22 (HIN1)
/ESC3/ALOW: U6.15 (PB1), U7.1 (LIN1)
/ESC3/BEMF_A: R10.6, R10.7, R30.2, U6.6 (PA0)
/ESC3/BEMF_B: R18.4, R18.7, R35.2, U6.10 (PA4)
/ESC3/BEMF_C: R18.2, R18.5, R40.2, U6.11 (PA5)
/ESC3/BEMF_COM: R10.5, R18.1, R18.3, U6.7 (PA1)
/ESC3/BHIGH: U6.19 (PA9), U7.23 (HIN2)
/ESC3/BLOW: U6.14 (PB0), U7.2 (LIN2)
/ESC3/CHIGH: U6.18 (PA8), U7.24 (HIN3)
/ESC3/CLOW: U6.13 (PA7), U7.3 (LIN3)
/ESC3/FloatA: C41.1, Q13.S, Q14.D, R10.8, U7.18 (VS1); also elsewhere on the board
/ESC3/FloatB: C40.1, Q15.S, Q16.D, R18.8, U7.15 (VS2); also elsewhere on the board
/ESC3/FloatC: C39.1, Q17.S, Q18.D, R18.6, U7.12 (VS3); also elsewhere on the board
/ESC3/HO1: R47.1, U7.19 (HO1)
/ESC3/HO2: R52.1, U7.16 (HO2)
/ESC3/HO3: R57.1, U7.13 (HO3)
/ESC3/LO1: R48.1, U7.11 (LO1)
/ESC3/LO2: R53.1, U7.10 (LO2)
/ESC3/LO3: R58.1, U7.9 (LO3)
/ESC3/SWDCLK: TP5.1, U6.22 (PA14); also elsewhere on the board
/ESC3/SWDIO: TP6.1, U6.21 (PA13); also elsewhere on the board
/ESC3/VOLT_SENSE: R42.2, R43.1, U6.12 (PA6)
/dshot_3: R46.1; also elsewhere on the board
GND: C29.2, C31.2, C33.2, C42.2, Q14.S, Q16.S, Q18.S, R30.1, R35.1, R40.1, R43.2, R45.1, U6.16 (VSS), U6.29 (VSS), U7.6 (COM), U7.25 (COM); also elsewhere on the board
unnamed: Q13.G, R47.2
unnamed: Q14.G, R48.2
unnamed: Q15.G, R52.2
unnamed: Q16.G, R53.2
unnamed: Q17.G, R57.2
unnamed: Q18.G, R58.2
unnamed: R45.2, U6.1 (BOOT0)
unnamed: C31.1, U6.4 (NRST)
unnamed: R46.2, U6.25 (PB4)
unnamed: C41.2, U7.20 (VB1)
unnamed: C40.2, U7.17 (VB2)
unnamed: C39.2, U7.14 (VB3)

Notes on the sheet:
Low Output
Low Input
Mosfet Gate Driver
Place close to chip
MCU
Bulk Decoupling
Back EMF
Mosfets
High Input
High Output

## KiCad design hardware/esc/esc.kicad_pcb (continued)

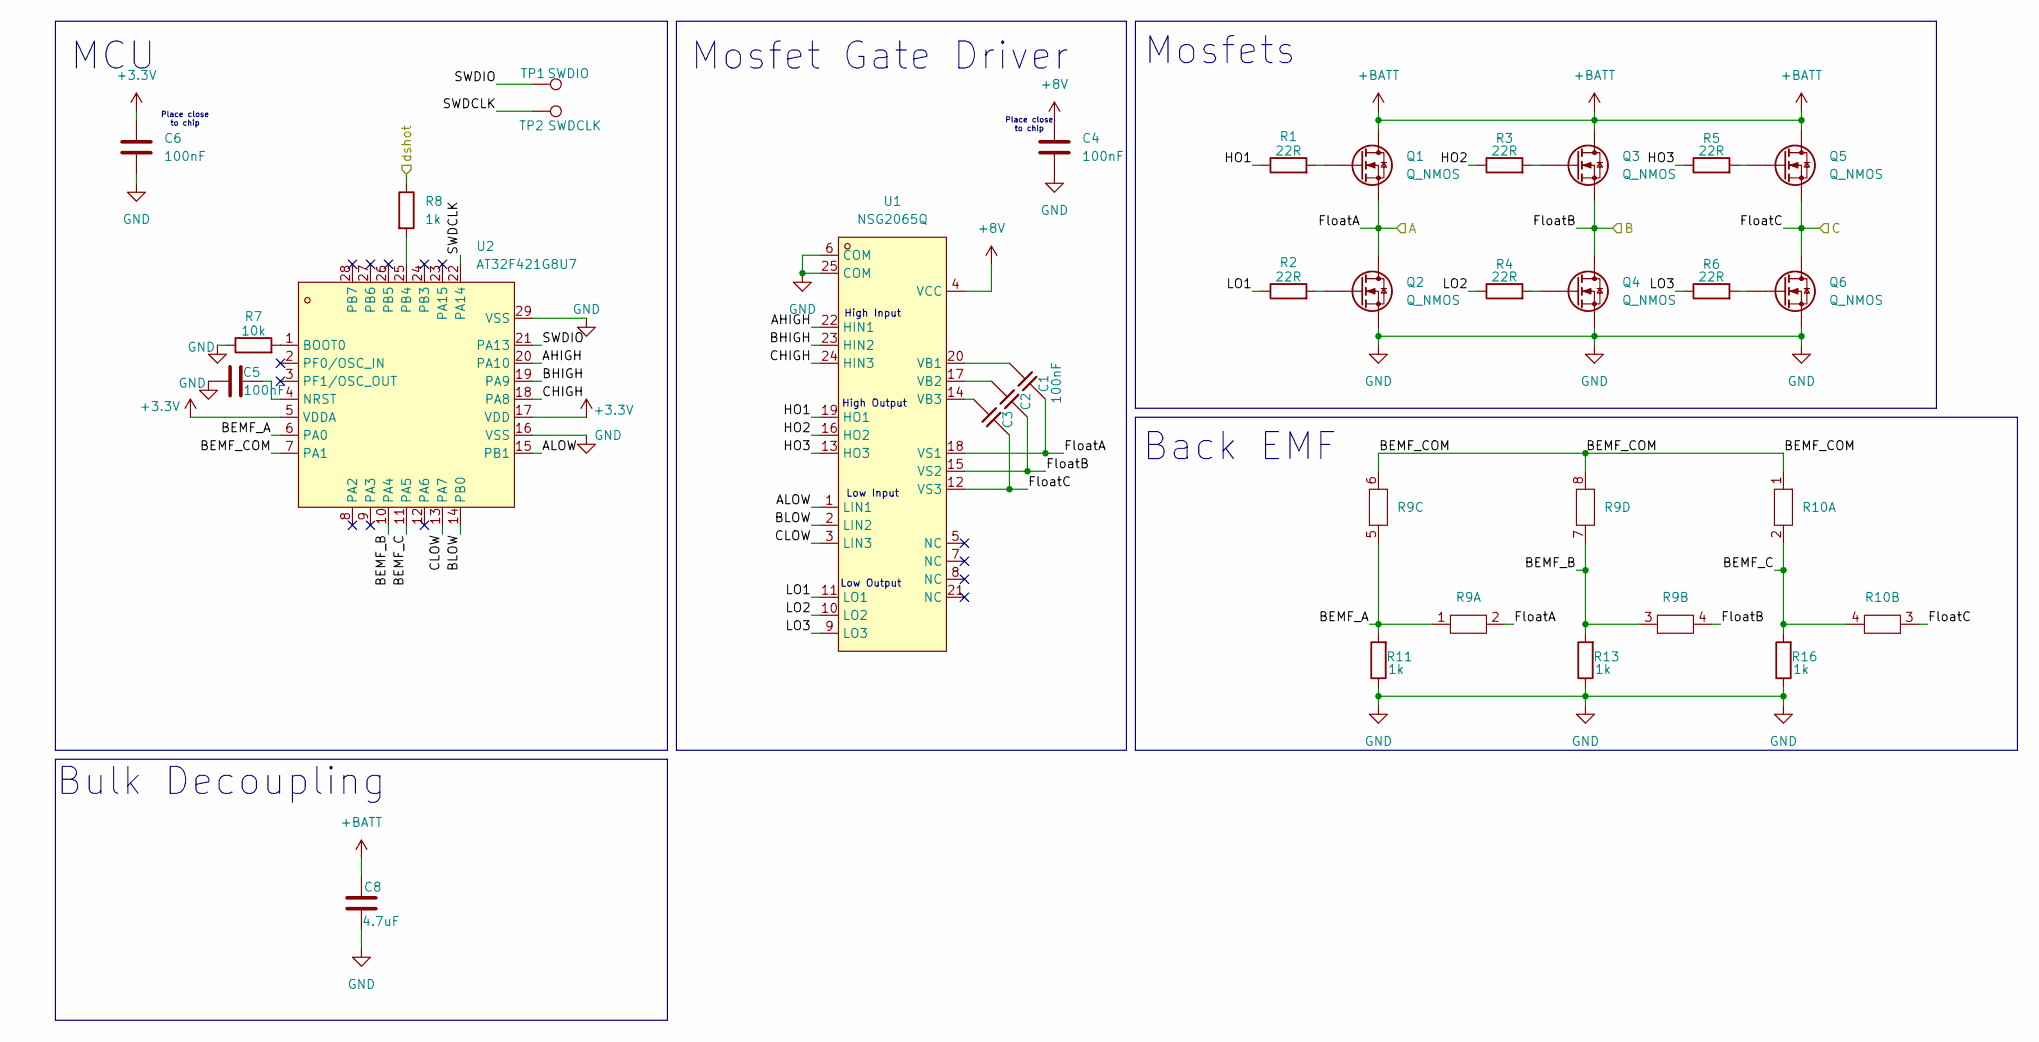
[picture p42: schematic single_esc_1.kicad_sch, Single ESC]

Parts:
C1, C2, C3, C4, C5, C6: 100nF; C_0402_1005Metric
C8: 4.7uF; C_0603_1608Metric
Q1, Q2, Q3, Q4, Q5, Q6: Q_NMOS; POWERPAK-1212-8_L3.0-W3.0-P0.65-LS3.3-BL
R1, R2, R3, R4, R5, R6: 22R; R_0402_1005Metric
R7: 10k; R_0402_1005Metric
R8, R11, R13, R16: 1k; R_0402_1005Metric
R9, R10: RES_4D03_0603_3P2X1P6_ROH
TP1: SWDIO; TestPoint_Pad_D1.0mm
TP2: SWDCLK; TestPoint_Pad_D1.0mm
U1: NSG2065Q; QFN-24_L4.0-W4.0-P0.50-TL-EP2.8; LCSC Part C41414478
U2: AT32F421G8U7; QFN-28_L4.0-W4.0-P0.40-TL-EP2.4; LCSC Part C2765098

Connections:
+3.3V: C6.1, U2.5 (VDDA), U2.17 (VDD); also elsewhere on the board
+8V: C4.1, U1.4 (VCC); also elsewhere on the board
+BATT: C8.1, Q1.D, Q3.D, Q5.D; also elsewhere on the board
/ESC1/AHIGH: U1.22 (HIN1), U2.20 (PA10)
/ESC1/ALOW: U1.1 (LIN1), U2.15 (PB1)
/ESC1/BEMF_A: R9.1, R9.5, R11.2, U2.6 (PA0)
/ESC1/BEMF_B: R9.3, R9.7, R13.2, U2.10 (PA4)
/ESC1/BEMF_C: R10.2, R10.4, R16.2, U2.11 (PA5)
/ESC1/BEMF_COM: R9.6, R9.8, R10.1, U2.7 (PA1)
/ESC1/BHIGH: U1.23 (HIN2), U2.19 (PA9)
/ESC1/BLOW: U1.2 (LIN2), U2.14 (PB0)
/ESC1/CHIGH: U1.24 (HIN3), U2.18 (PA8)
/ESC1/CLOW: U1.3 (LIN3), U2.13 (PA7)
/ESC1/FloatA: C1.1, Q1.S, Q2.D, R9.2, U1.18 (VS1); also elsewhere on the board
/ESC1/FloatB: C2.1, Q3.S, Q4.D, R9.4, U1.15 (VS2); also elsewhere on the board
/ESC1/FloatC: C3.1, Q5.S, Q6.D, R10.3, U1.12 (VS3); also elsewhere on the board
/ESC1/HO1: R1.1, U1.19 (HO1)
/ESC1/HO2: R3.1, U1.16 (HO2)
/ESC1/HO3: R5.1, U1.13 (HO3)
/ESC1/LO1: R2.1, U1.11 (LO1)
/ESC1/LO2: R4.1, U1.10 (LO2)
/ESC1/LO3: R6.1, U1.9 (LO3)
/ESC1/SWDCLK: TP2.1, U2.22 (PA14); also elsewhere on the board
/ESC1/SWDIO: TP1.1, U2.21 (PA13); also elsewhere on the board
/dshot_1: R8.1; also elsewhere on the board
GND: C4.2, C5.2, C6.2, C8.2, Q2.S, Q4.S, Q6.S, R7.1, R11.1, R13.1, R16.1, U1.6 (COM), U1.25 (COM), U2.16 (VSS), U2.29 (VSS); also elsewhere on the board
unnamed: Q1.G, R1.2
unnamed: Q2.G, R2.2
unnamed: Q3.G, R3.2
unnamed: Q4.G, R4.2
unnamed: Q5.G, R5.2
unnamed: Q6.G, R6.2
unnamed: C1.2, U1.20 (VB1)
unnamed: C2.2, U1.17 (VB2)
unnamed: C3.2, U1.14 (VB3)
unnamed: R7.2, U2.1 (BOOT0)
unnamed: C5.1, U2.4 (NRST)
unnamed: R8.2, U2.25 (PB4)

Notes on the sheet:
High Output
Mosfet Gate Driver
High Input
MCU
Place close to chip
Low Output
Mosfets
Low Input
Back EMF
Bulk Decoupling

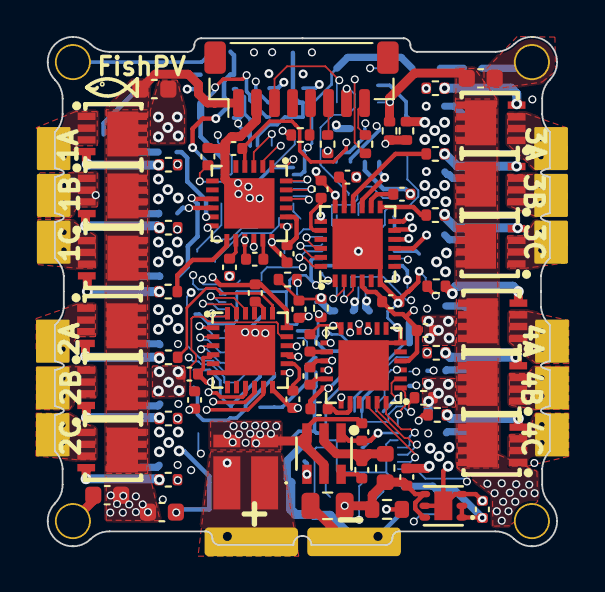
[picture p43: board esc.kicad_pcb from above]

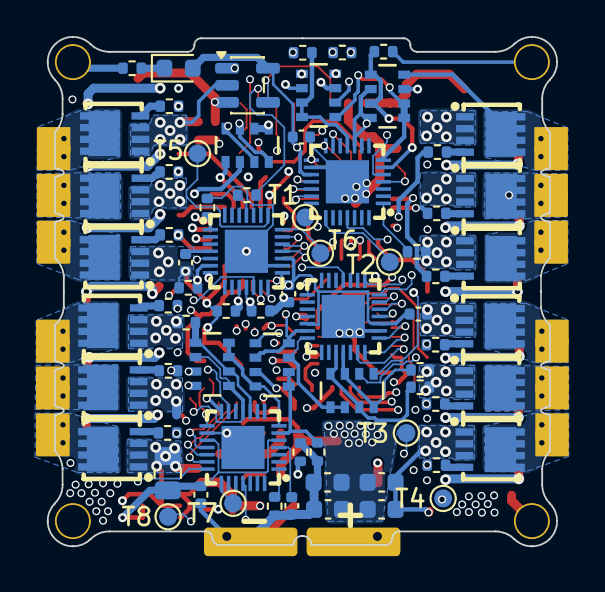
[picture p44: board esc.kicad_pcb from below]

Board: 6 copper layers, 28.3 x 28.3 mm, 141 parts (71 on the bottom side), 147 nets.

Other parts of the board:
T1, T3, T6, T8: SWDIO; TestPoint_Pad_D1.0mm
T2, T4, T5, T7: SWDCLK; TestPoint_Pad_D1.0mm

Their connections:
/ESC1/SWDCLK: T2.1 (1_1); also elsewhere on the board
/ESC1/SWDIO: T1.1 (1_1); also elsewhere on the board
/ESC2/SWDCLK: T4.1 (1_1); also elsewhere on the board
/ESC2/SWDIO: T3.1 (1_1); also elsewhere on the board
/ESC3/SWDCLK: T5.1 (1_1); also elsewhere on the board
/ESC3/SWDIO: T6.1 (1_1); also elsewhere on the board
/ESC4/SWDCLK: T7.1 (1_1); also elsewhere on the board
/ESC4/SWDIO: T8.1 (1_1); also elsewhere on the board

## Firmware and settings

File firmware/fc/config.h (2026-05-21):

/*
 * This file is part of Betaflight.
 *
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
 * See the GNU General Public License for more details.
 *
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
 * If not, see <http://www.gnu.org/licenses/>.
 */

#pragma once

#define FC_TARGET_MCU     STM32F405

/* TODO RENAME BOARD */
#define BOARD_NAME        MYDRONEIDK
#define MANUFACTURER_ID   CUST

#define USE_ACC
#define USE_GYRO

#define USE_ACC_SPI_ICM42688P
#define USE_GYRO_SPI_ICM42688P
// Enable gyro clkin timer
#define USE_GYRO_CLKIN

#define USE_BARO
#define USE_BARO_BMP280

// Technically wrong flash chip but the other define
// is for quad/octo spi
#define USE_FLASH
#define USE_FLASH_M25P16

#define USE_MAX7456

// I/O
#define LED0_PIN             PC15
#define LED1_PIN             PC14
// DISABLED FOR NOW AS UNTESTED, MAY NEED TO ADD MOSFET
// #define BEEPER_PIN           PC13
// #define BEEPER_INVERTED

// ACC/GYRO SPI 1
#define USE_SPI_GYRO
#define GYRO_1_EXTI_PIN      PC4
#define GYRO_1_CS_PIN        PA4
#define GYRO_1_SPI_INSTANCE  SPI1
#define GYRO_1_CLKIN_PIN     PB8
#define GYRO_1_ALIGN         CW0_DEG

#define SPI1_SCK_PIN         PA5
#define SPI1_SDI_PIN         PA6
#define SPI1_SDO_PIN         PA7

// FLASH SPI 2
#define SPI2_SCK_PIN         PB13
#define SPI2_SDI_PIN         PB14
#define SPI2_SDO_PIN         PB15

#define FLASH_CS_PIN         PB12
#define FLASH_SPI_INSTANCE   SPI2

// OSD SPI 3
#define SPI3_SCK_PIN         PC10
#define SPI3_SDI_PIN         PC11
#define SPI3_SDO_PIN         PB5

#define MAX7456_SPI_CS_PIN   PA15
#define MAX7456_SPI_INSTANCE SPI3

// ADC
#define USE_ADC
#define ADC_VBAT_PIN         PC1
// #define ADC_RSSI_PIN         PC2
#define ADC_CURR_PIN         PC2
#define ADC_INSTANCE         ADC1

// UART PORTS
// UART1 - ELRS
#define UART1_TX_PIN         PB6
#define UART1_RX_PIN         PB7

// UART2 
// #define UART2_TX_PIN         PA2
// #define UART2_RX_PIN         PA3

// UART3 
// #define UART3_TX_PIN         PB10
// #define UART3_RX_PIN         PB11

// UART4 
#define UART4_TX_PIN         PA0
#define UART4_RX_PIN         PA1

// UART5 
#define UART5_TX_PIN         PC12
#define UART5_RX_PIN         PD2

// UART6
// #define UART6_TX_PIN         PC6
// #define UART6_RX_PIN         PC7

// TIMERS
#define TIMER_PIN_MAPPING \
    TIMER_PIN_MAP( 0, PA9 , 1,  1) \
    TIMER_PIN_MAP( 1, PA8 , 1,  1) \
    TIMER_PIN_MAP( 2, PC9 , 1,  0) \
    TIMER_PIN_MAP( 3, PC8 , 1,  0) \
    TIMER_PIN_MAP( 4, PB8 , 3, -1)

// MOTORS PINOUT
#define MOTOR1_PIN           PA9
#define MOTOR2_PIN           PA8
#define MOTOR3_PIN           PC9
#define MOTOR4_PIN           PC8

#define ADC1_DMA_OPT         1

// BARO I2C
#define BARO_I2C_INSTANCE I2CDEV_2
#define MAG_I2C_INSTANCE I2CDEV_2

#define I2C1_SCL_PIN         PB10
#define I2C1_SDA_PIN         PB11

// USERS
// #define PINIO1_PIN           PB1
// #define PINIO1_BOX 40
// #define PINIO1_CONFIG 129

// DEFAULTS
#define DEFAULT_BLACKBOX_DEVICE         BLACKBOX_DEVICE_FLASH
#define DEFAULT_CURRENT_METER_SOURCE    CURRENT_METER_ADC
#define DEFAULT_VOLTAGE_METER_SOURCE    VOLTAGE_METER_ADC
#define DEFAULT_VOLTAGE_METER_SCALE     102
#define DEFAULT_DSHOT_BURST             DSHOT_DMAR_OFF
#define DEFAULT_DSHOT_BITBANG           DSHOT_BITBANG_OFF
#define SYSTEM_HSE_MHZ                  8

// DISABLED
// #define INVERTER_PIN_UART1   PC0
// #define ESCSERIAL_PIN        PB9

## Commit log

2026-04-02 ESC Layout try 1
    [esc.kicad_pcb]
2026-04-02 journal for 2nd april
    [esc.kicad_pcb]
2026-04-03 redo layout and new board outline
    [BoardOutlineV1.dxf, bom.csv, bom.ods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]
2026-04-05 board pcb + res arrays
    [bom.ods, esc.kicad_pcb, esc.kicad_sch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]
2026-04-05 Sync for windows
    [esc.kicad_pcb]
2026-04-07 Routing done!
    [BoardOutlineV2.dxf, esc.kicad_pcb, esc.kicad_sch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]
2026-04-11 start flight controller
    [bom.csv, designators.csv, esc.kicad_pcb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]
2026-04-13 More work on FC
    [fc.kicad_sch]
2026-05-21 Finished boards, restructured, readme, sim, and more!
    Former-commit-id: 1faa8c61b1a9c7058c908202a6c3d018e8ff8ca2
    [2-panel-sliding-window_720879d7-e439-499d-bc9f-fc70603a9b93.blend, BoardOutlineV1.dxf, BoardOutlineV2.dxf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]
2026-05-21 lfs
    Former-commit-id: d8ebaec57af61f51661c7e7436063da323a8d36b
    [2-panel-sliding-window_720879d7-e439-499d-bc9f-fc70603a9b93.blend, audio-control_2K_472523a6-e4d7-4b51-b55d-0612182fcbb2.blend, bed_2K_a45201e4-48fd-4889-ac00-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]
2026-05-30 Add wiring diagram, zine, more readme, bom
    Former-commit-id: 3e30fac0ecf017dfad40331f47e922149ad91b9f
    [battery-support.step, battery-support.stl, bom.ods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]
2026-05-30 try to fix lfs
    [render.blend]
2026-05-30 update bom totals
    [combined.ods]

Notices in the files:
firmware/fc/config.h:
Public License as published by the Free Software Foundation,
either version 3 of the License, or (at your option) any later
